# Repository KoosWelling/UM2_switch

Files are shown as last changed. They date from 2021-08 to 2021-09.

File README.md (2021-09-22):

# UM2_switch
Transform your Ultimaker 2+ into dual extrusion system.

Time to upgrade my UM2 to dual extrusion printer. I got this switching mechanism idea already a year ago, but never took time to realize. Since the first tests seems to be promising, it's time to share this upgrade. It's working with a simple cam-plate, which is moving both nozzles at the same time. The cam-plate is bi-stable, by using the existing springs which also hold the teflon isolator in place.

Benefits of this modification, besides enabling 2 material prints:
- Simple modification on the existing hardware
- Switching is done above bed clips, so no loss of additional print space
- Modification works both on UM2 and UM2+ 

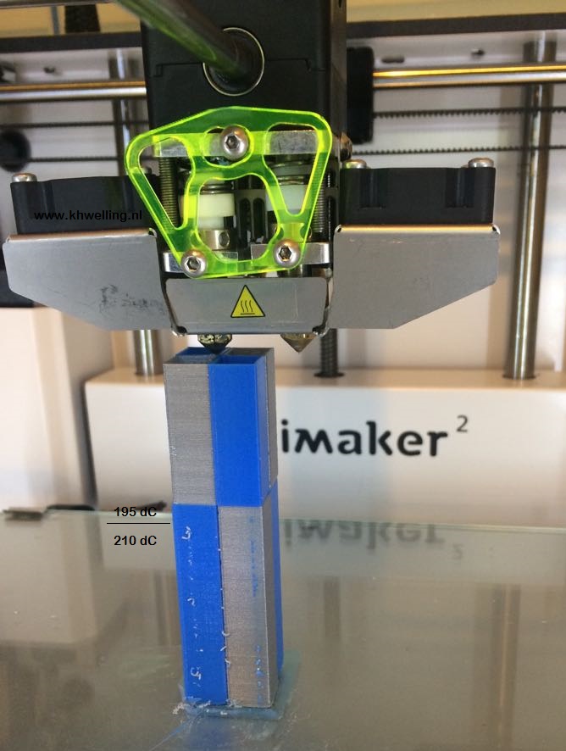
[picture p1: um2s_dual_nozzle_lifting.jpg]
UM2s dual nozzle lifting


## Hardware
Of course you will need a <a href="https://ultimaker.com/en/products/extrusion-upgrade-kit" target="blank">second extrusion train</a>.
Besides that, the good news is, the most important parts to be modified are already in your UM2. Basically you need to cut the bottom-plate in half, creating 2 levers. Modify them, so they could rotate. Bolt a bearing (W 627/3-2Z) on the front side of the top plate, used for the switch plate. 
The only part left is the cam-plate. 

In my case it's a laser cuted PolyStyreen plate. It surprisingly surveys already multiple days, none stop printing with 240 degrees nozzles & 70 degrees heated build plate.

Then on both sides of the printer, you need a 'switching-block'. Just a simple printed part should do the job. An other interesting working solution: use the UM side bearings as switching location. Then you only need a 'X' movement to do the switching action. But I leave this to your own imagination.

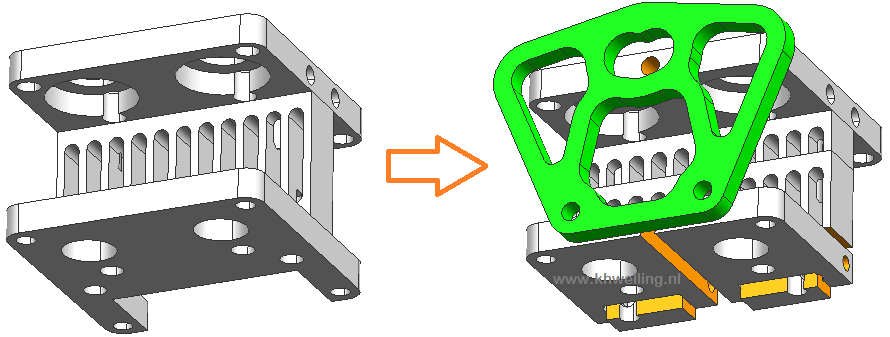
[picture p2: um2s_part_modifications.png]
UM2 parts modified

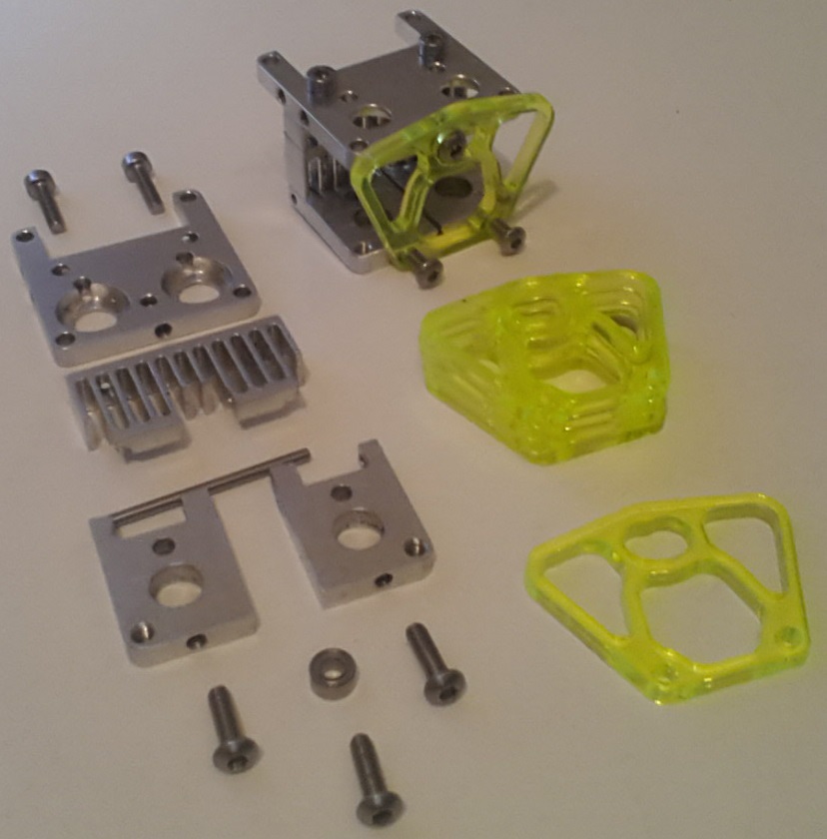
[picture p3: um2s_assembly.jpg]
UM2s assembly


## Firmware
The most important thing in the firmware, is tell your UM2(+) to use a second nozzle. There are different options:

* DIY: so download the right Marlin firmware from Github and change the number of extruders.
If you don't know how to do this, search the <a href="https://ultimaker.com/en/community/hardware" target="blank">UM</a> forum for more info.

* You might try this marlin version. 

* Or upload changes I made, yourselfs:
  * file: configuration.h
    - #define EXTRUDERS 2
  * file: UltiLCD2_menau_print.cpp:
    - #define HEATUP_POSITION_COMMAND "G1 F12000 X110 Y10"
    - Prime position = "G28 X115 Y10"
    - Pause position = "M601 X115 Y10 Z%i L%i"
These positions are changed, so when you do switching in the corner, you don't want to hit these positions while priming/pausing..

## Cura
Cura <3.4

Copy Cura definiions from the provided zipfile.
If you use newer version of Cura (most likely), you need to debug a bit.
If you have a working version, please upload/send!

Cura >3.4???

Within the *ultimaker2s_1st.def.json* extruder definition, it is/was possible to add an 'override':
* **"machine_extruder_start_code": { "default_value": "G0 F9000 X219 Y17.5\nG0 F1000 X223\nG0 F9000 X219" }**

This is basically the switching code, which will automatically implemented when slicing an object.

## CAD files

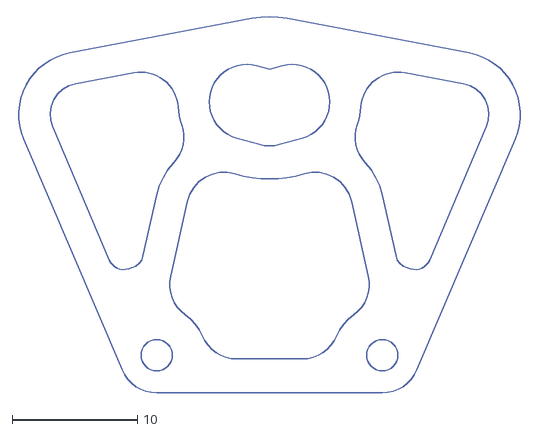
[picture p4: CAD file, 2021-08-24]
um2_cam_plate_switching_02C3.dxf
40.4 x 30.0

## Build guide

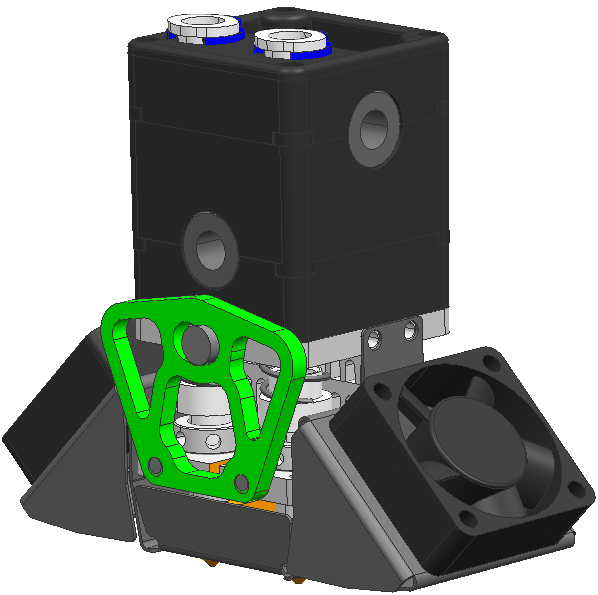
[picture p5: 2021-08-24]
um2s_modified_printhead.png
